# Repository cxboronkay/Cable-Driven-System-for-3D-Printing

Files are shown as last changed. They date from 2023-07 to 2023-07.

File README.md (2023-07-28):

# Cable-Driven-System-for-3D-Printing
Please see the powerpoint "Large scale 3d printing with CDPR" for instructional information and electronics schematics before use.

Design files and necessary programs for running the CDPR machine can be found here, as well as simple example G-code programs. Assembly is uploaded as a SolidWorks assembly with all necessary parts. All 3D printed parts are also uploaded as STEPs and STLs, as well as one STEP version of the assembly as a whole.
CDPRassem


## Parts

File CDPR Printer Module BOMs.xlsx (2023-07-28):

Single Pulley Module
Part Name | Qty | Process/Material | Remark
Table base | 1 | 3D printed (PLA)
5mm Flanged Bearing (16mm OD) | 1 | -
Small scale pulley | 1 | 3D printed (PLA)
Pulley mount | 2 | 3D printed (PLA) | Designed for PLA although mine were printed in PETG
6mm flanged bearing (13mm OD) | 2 | -
Encoder mount | 1 | 3D printed (PLA)
6mm d-shaft (L 55mm) | 1 | 3D printed (PLA) | Steel shaft can be purchased but often run oversized for fitting in bearing
Rope guide | 1 | 3D printed (PLA)
AS5600 magnetic encoder | 1 | - | and accompanying magnet (will be fixed to end of shaft)
M5 eyebolt (L 3.5 cm) | 1 | -
6mm washers (1.2mm thickness) | 6 | Nylon
M5 socket head bolt (L 16mm) | 9 | -
M5 socket head bolt (L 18mm) | 3 | -
M3 screw (L 5mm) | 2 | -
M5 washers (1mm thickness) | 8 | Nylon | Or can use equivalent 8mm spacer
M5 washers | 7 | Steel
M5 hex nuts | 13 | -
M3 hex nuts | 2 | -
M5 extrusion insert nut | 1 | - | If mounting module to aluminum extrusion
Single Winch Module
Part Name | Qty | Process/Material | Remark
NEMA 17 stepper motor | 1 | -
Motor mount | 1 | 3D printed (PLA)
Winch bearing mount | 1 | 3D printed (PLA)
2020 T-slot profile bar (L 60mm) | 1 | Aluminum
5mm to 8mm shaft coupler | 1 | -
8mm flanged bearing (16mm OD) | 1 | -
Winch spool | 1 | 3D printed (PLA)
8mm d-shaft (L 55mm) | 1 | 3D printed (PLA)
M5 eyebolt (L 3.5 cm) | 1 | -
Extrusion corner bracket | 1 | -
M8 washer (1.4mm thickness) | 1 | Nylon
M5 bolt (L 8mm) | 8 | -
M5 extrusion insert nut | 9 | - | If mounting module to aluminum extrusion
M3 screw (L 10mm) | 2 | -

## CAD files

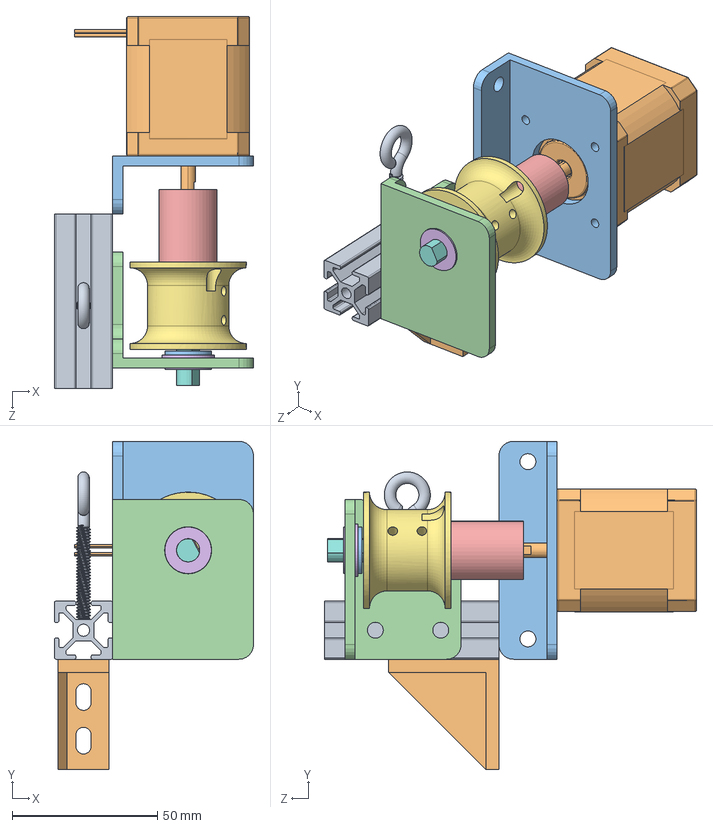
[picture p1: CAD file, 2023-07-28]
SW Design Files/Winch module.SLDASM
68.5 x 113.0 x 128.0 mm
2020 T-slot profile bar
NEMA motor 17HS19-2004S1
motor (NEMA) mount
winch bearing mount
5mm to 8mm coupler
8mm flange bearing
winch spool 2
8mm d shaft
M5 eyebolt (stand-in)
6mm corner bracket
M8 nylon washer

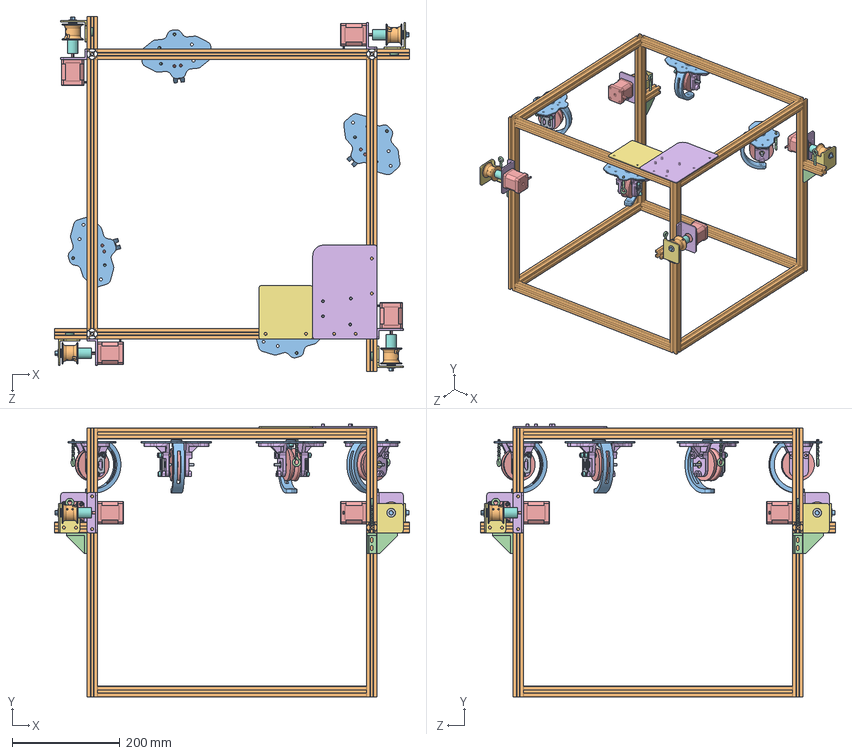
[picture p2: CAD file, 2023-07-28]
SW Design Files/CDPR printer assembly.SLDASM
660.0 x 507.5 x 660.0 mm
2020 T-slot profile bar x 16
table_base_v4 x 4
5mm flanged bearing x 4
Small-scale pulley x 4
Pulley mount x 8
6mm flanged linear x 8
Encoder mount AS5600 x 4
91290A238_Alloy Steel Socket Head Screw x 16
6mm d-shaft x 4
5mm hex nut x 12
ropeguide_v3 x 4
M5 eyebolt (stand-in) x 8
NEMA motor 17HS19-2004S1 x 4
motor (NEMA) mount x 4
winch bearing mount x 4
5mm to 8mm coupler x 4
8mm flange bearing x 4
winch spool 2 x 4
8mm d shaft x 4
6mm corner bracket x 4
M8 nylon washer x 4
electronics_board
second_electronics_board

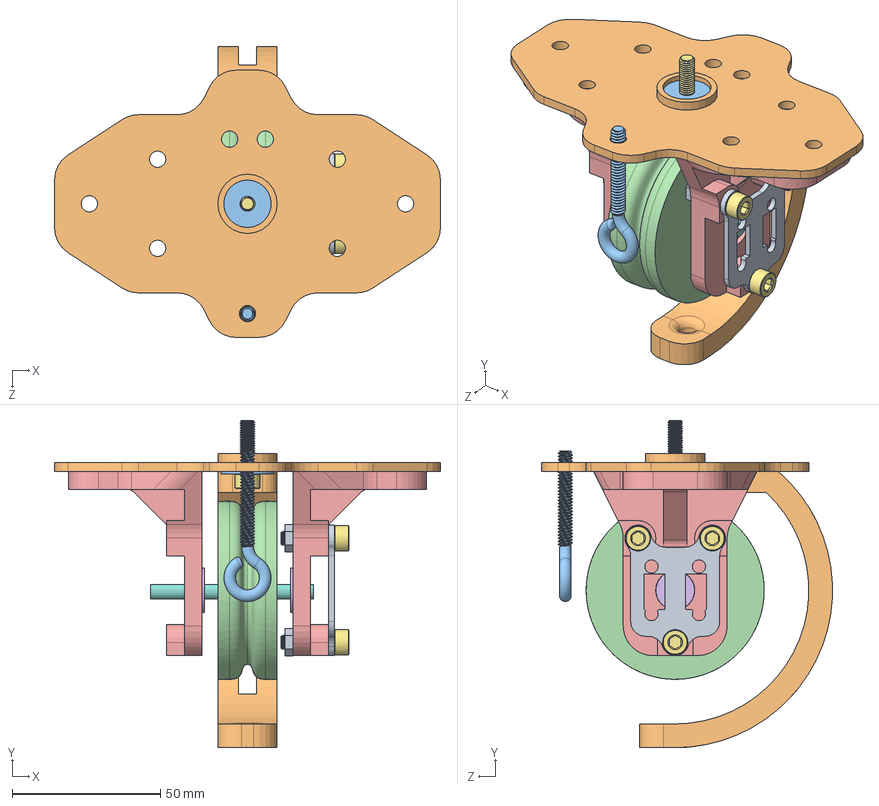
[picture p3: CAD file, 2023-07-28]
SW Design Files/Pulley encoder module.SLDASM
130.0 x 110.2 x 97.9 mm
table_base_v4
5mm flanged bearing
Small-scale pulley
Pulley mount x 2
6mm flanged linear x 2
Encoder mount AS5600
91290A238_Alloy Steel Socket Head Screw x 4
6mm d-shaft
5mm hex nut x 3
ropeguide_v3
M5 eyebolt (stand-in)

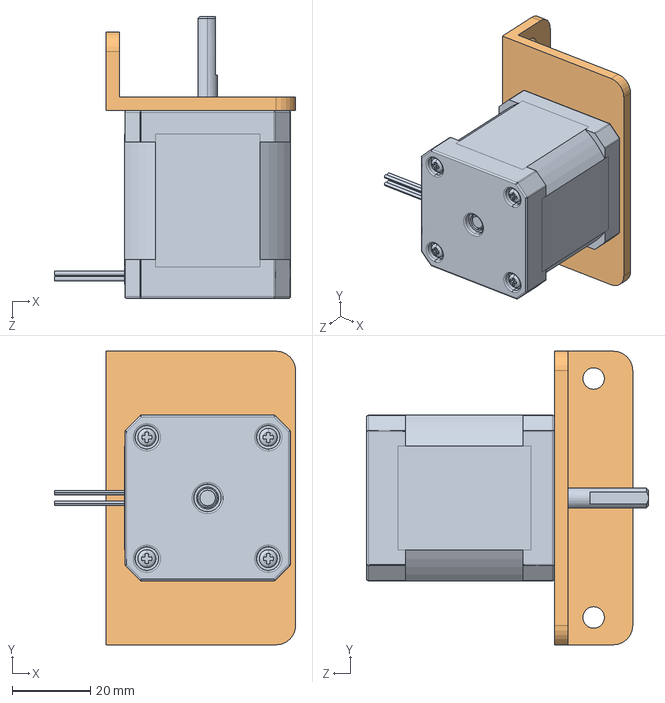
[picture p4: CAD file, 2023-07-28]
SW Design Files/motor assembly.SLDASM
61.7 x 75.0 x 72.0 mm
NEMA motor 17HS19-2004S1
motor (NEMA) mount

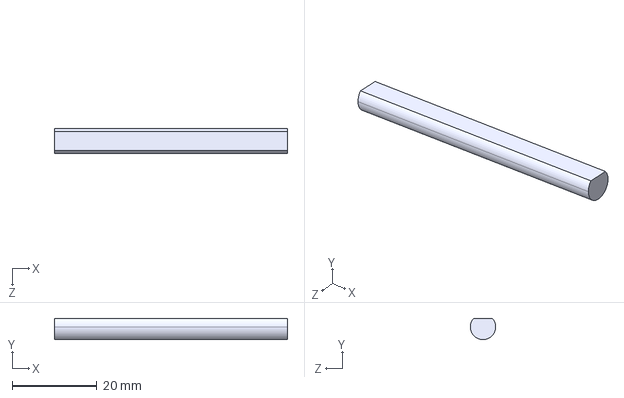
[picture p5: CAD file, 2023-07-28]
STEP files/6mm d-shaft.STEP
55.0 x 5.00 x 6.00 mm

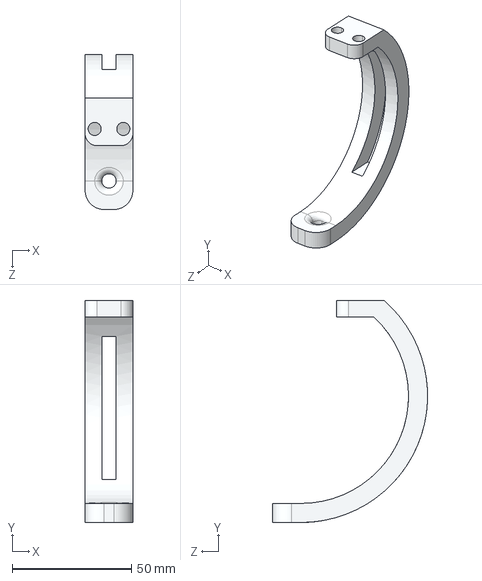
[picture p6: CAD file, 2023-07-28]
STEP files/ropeguide_v3.STEP
20.0 x 93.0 x 65.0 mm

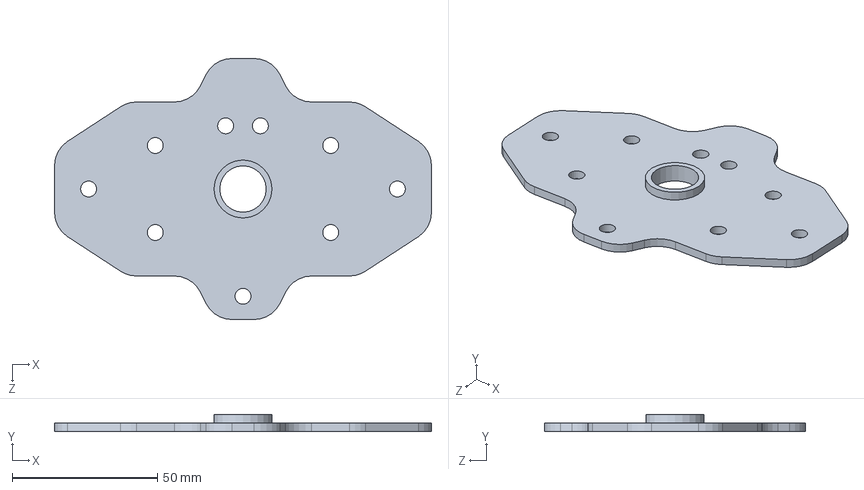
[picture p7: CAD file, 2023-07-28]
SW Design Files/table_base_v4.SLDPRT
130.0 x 6.00 x 90.0 mm

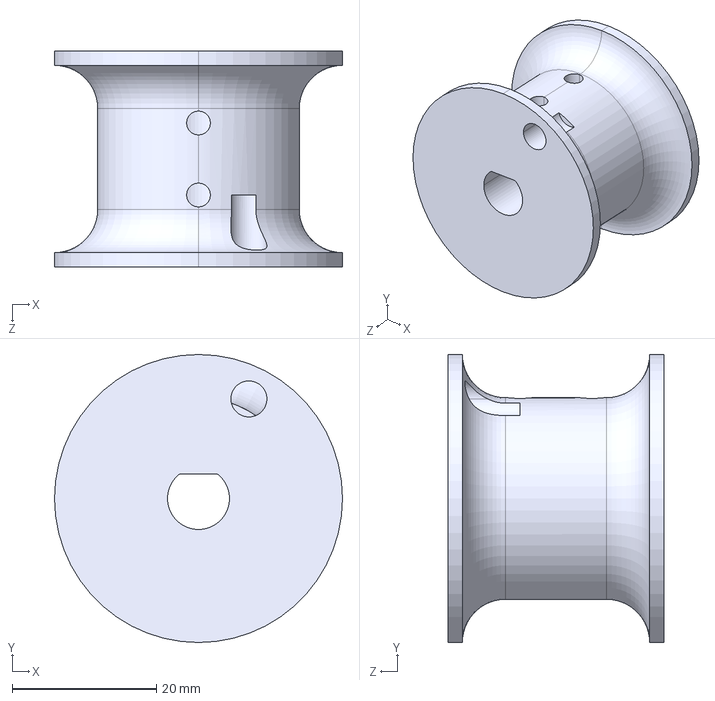
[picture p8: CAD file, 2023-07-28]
STEP files/winch spool 2.STEP
40.0 x 40.0 x 30.0 mm

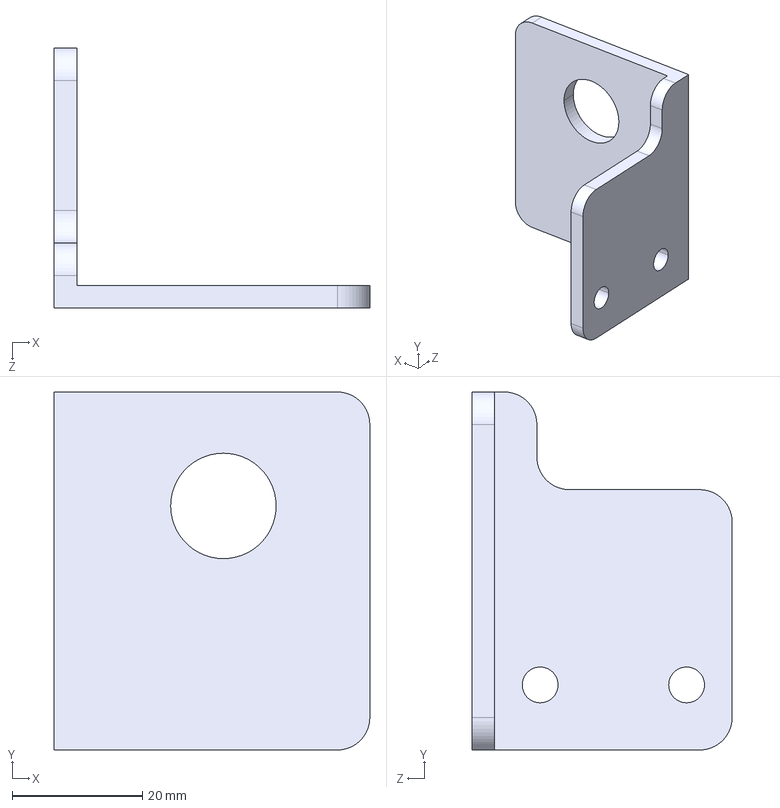
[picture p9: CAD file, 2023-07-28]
STEP files/winch bearing mount.STEP
48.5 x 55.0 x 40.0 mm

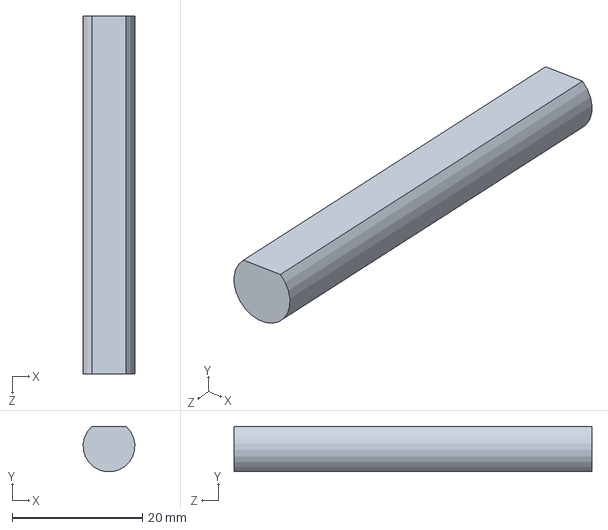
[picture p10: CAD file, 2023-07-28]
SW Design Files/8mm d shaft.SLDPRT
7.95 x 6.97 x 55.0 mm

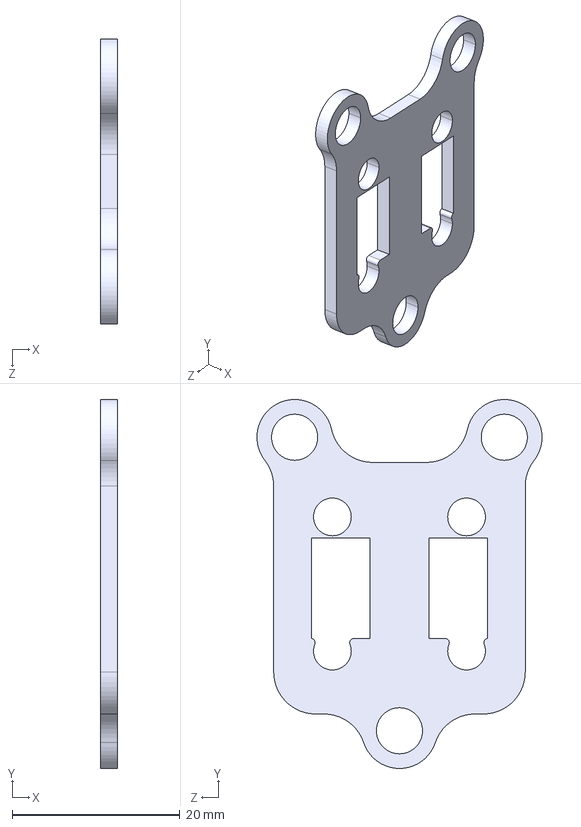
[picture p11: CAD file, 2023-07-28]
STEP files/Encoder mount AS5600.STEP
2.00 x 44.0 x 34.0 mm

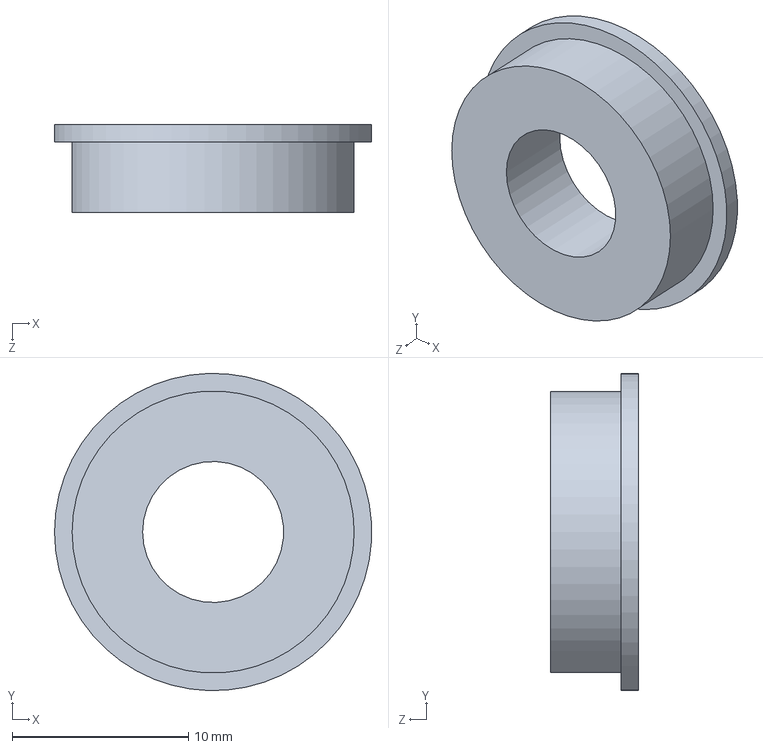
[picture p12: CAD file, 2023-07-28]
SW Design Files/8mm flange bearing.SLDPRT
18.0 x 18.0 x 5.00 mm

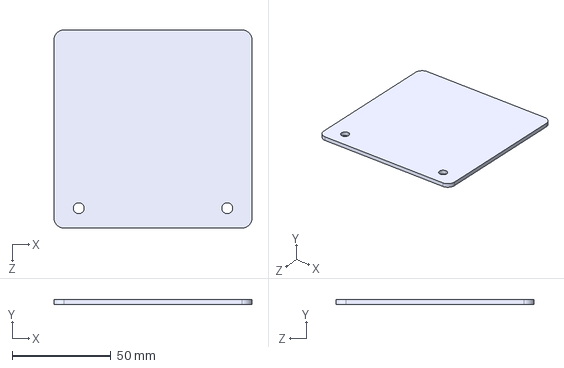
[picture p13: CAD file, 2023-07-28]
STEP files/second_electronics_board.STEP
100.0 x 2.50 x 100.0 mm

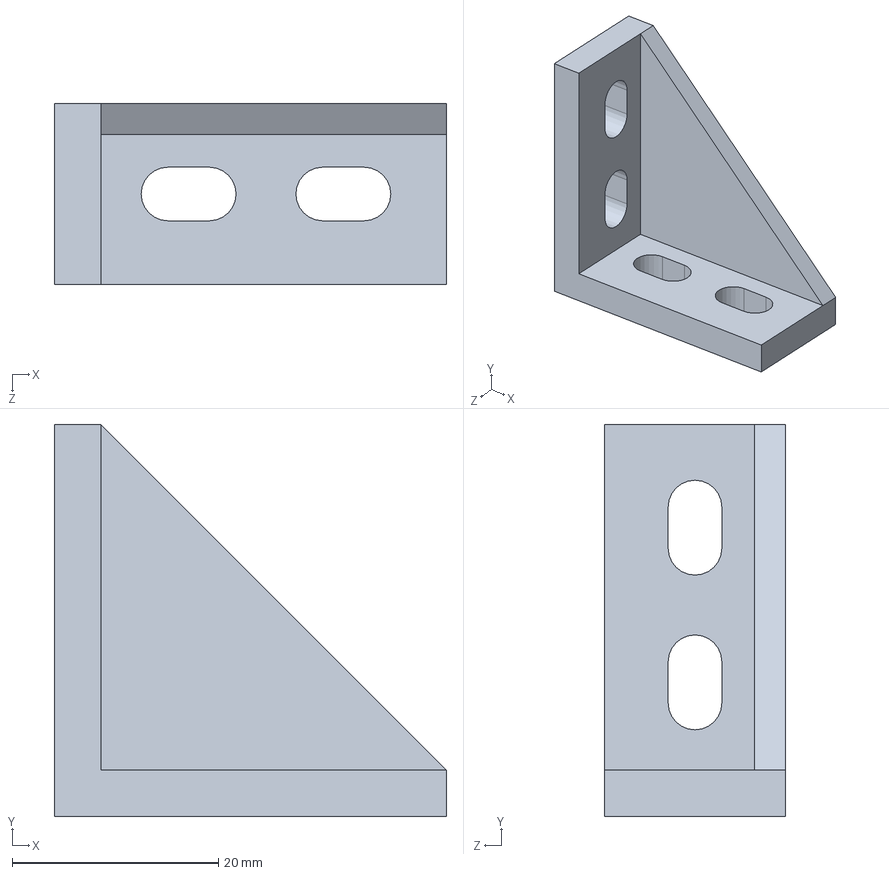
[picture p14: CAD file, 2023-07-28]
SW Design Files/6mm corner bracket.SLDPRT
38.0 x 38.0 x 17.5 mm

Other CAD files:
SW Design Files/6mm d-shaft.SLDPRT
SW Design Files/winch spool 2.SLDPRT
SW Design Files/Encoder mount AS5600.SLDPRT
STEP files/table_base_v4.STEP
STEP files/8mm d shaft.STEP
STEP files/Pulley mount.STEP
STEP files/Small-scale pulley.STEP
STEP files/electronics_board.STEP
STEP files/motor (NEMA) mount.STEP
STL Files/6mm d-shaft.STL
STL Files/8mm d shaft.STL
STL Files/Encoder mount AS5600.STL
STL Files/Pulley mount.STL
STL Files/Small-scale pulley.STL
STL Files/electronics_board.STL
STL Files/motor (NEMA) mount.STL
STL Files/ropeguide_v3.STL
STL Files/second_electronics_board.STL
STL Files/table_base_v4.STL
STL Files/winch bearing mount.STL
STL Files/winch spool 2.STL
SW Design Files/2020 T-slot profile bar.SLDPRT
SW Design Files/5mm flanged bearing.SLDPRT
SW Design Files/5mm hex nut.SLDPRT
SW Design Files/5mm to 8mm coupler.SLDPRT
SW Design Files/6mm flanged linear.SLDPRT
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

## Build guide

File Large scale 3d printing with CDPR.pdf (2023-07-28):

# Large scale 3d printing with CDPR

Cadence Boronkay

# Research, planning, scope

# Design goals + constraints

- Scalable
- Modular for in situ applications
- Precision satisfactory for 3d printing
- Visually/aesthetically appealing

# Previous work

- CDPR robots have been used at large scales (eg. construction), but typically for pick and place purposes, rather than additive manufacturing.
- Some 3d CDPR printers have been built at smaller scales, and with less modularity (fully constrained, many cables, fixed winch locations).
- There is a literature available on fully constrained CDPR printers but much less on underactuated (cable suspended) CDPRs.

# CDPR constraining

- m = number of cables, n = degrees of freedom
- m < n + 1 : under-constrained/underactuated (cable suspended)
- m = n + 1 : fully constrained
- m > n + 1 : redundantly constrained
- For 6 DOFs (full control of position and orientation), 8 cables are typically used.
- This is more complex, as one must avoid cable-cable and cable-end effector interference.

# CDPR constraining (cable arrangements)

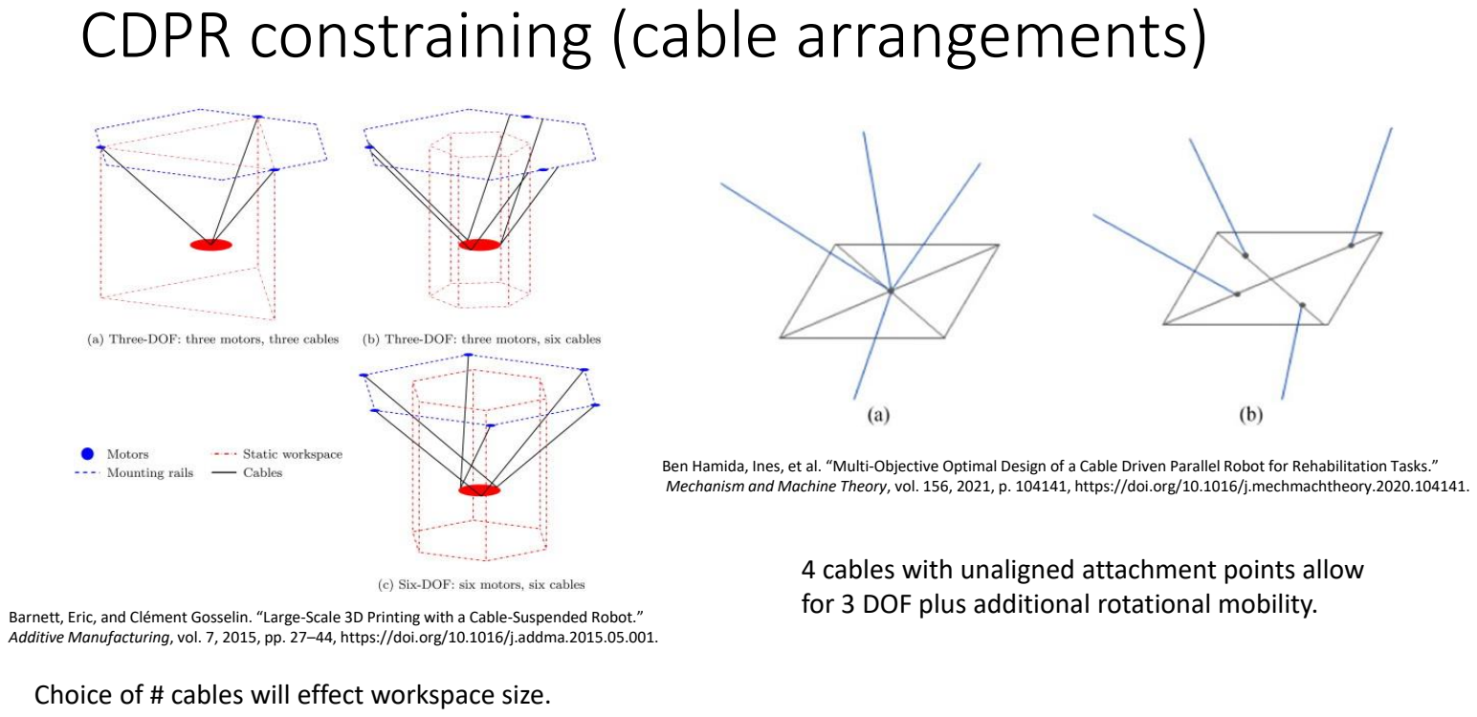
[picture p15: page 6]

Barnett, Eric, and Clément Gosselin. “Large-Scale 3D Printing with a Cable-Suspended Robot.” Additive Manufacturing, vol. 7, 2015, pp. 27–44, https://doi.org/10.1016/j.addma.2015.05.001.

Ben Hamida, Ines, et al. “Multi-Objective Optimal Design of a Cable Driven Parallel Robot for Rehabilitation Tasks.” Mechanism and Machine Theory, vol. 156, 2021, p. 104141, https://doi.org/10.1016/j.mechmachtheory.2020.104141.

4 cables with unaligned attachment points allow for 3 DOF plus additional rotational mobility.

Choice of # cables will effect workspace size.

# Controls

- Encoder options
- Encoder on motor/winch (will have error due to irregular winch diameter from cable spooling)
- *Rotary encoder on pulley (requires no cable slip on pulley, nonaxial forces due to the pulley on the encoder shaft could be problematic)
- Draw wire/cable pull encoder (limits scale-up, maximum draw length of encoder determines possible cable travel).
- Still researching software options for trajectory control/path generation from G-code.
- WireX, Hangprinter…

# Initial design sketching

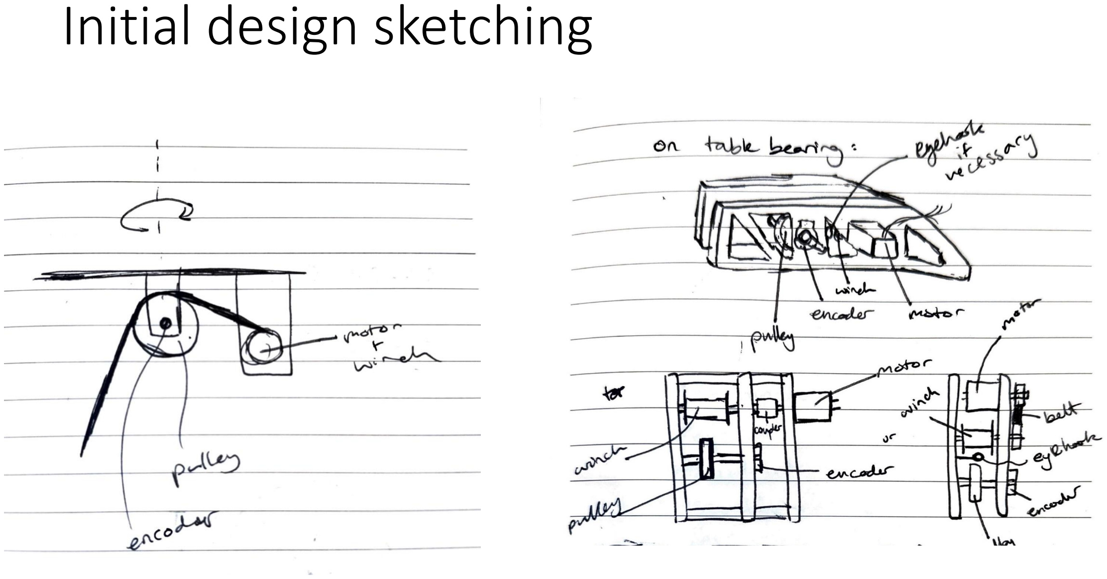
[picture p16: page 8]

# Design Considerations

- Pulley
- U-groove
- Eyehook to guide cable (prevent derailing)
- For encoder, cable must not slip on pulley (pulley needs to rotate with cable the entire time)
- Rubber coating? High traction material?
- If slippage is unavoidable, encoder could be moved to separate measuring wheel. (still need to somehow prevent slippage -> maybe dual-side wheels?)
- Check mechanical + dynamic calculations: need weight of end-effector, pulley material for friction coefficient, motor torque, etc.

# Design Considerations

- Turntable
- Probably best to put pulley on a table bearing - more accurate cable length measurements and less non-axial loads on cable and pulley. (Expected to be more significant on large-scale).
- Put entire module on turntable or just pulley?
- I think more entire is more modular and elegant, but possibly unnecessary).
- Table bearing axis of rotation needs to be centered above last point of contact (pulley) for controls. (Parametric measurements done from here too).

# Planning

- Small-scale prototype design, continue controls research
- Fabricate prototype, assembly 1 module (module = 1 set of motor/winch/pulley)
- Test module
- Revision
- Fabricate + assemble m modules
- Assemble m cable system
- Test system (small scale CDPR)
- Revise
- Work on scale-up of module

# Magnetic position encoder

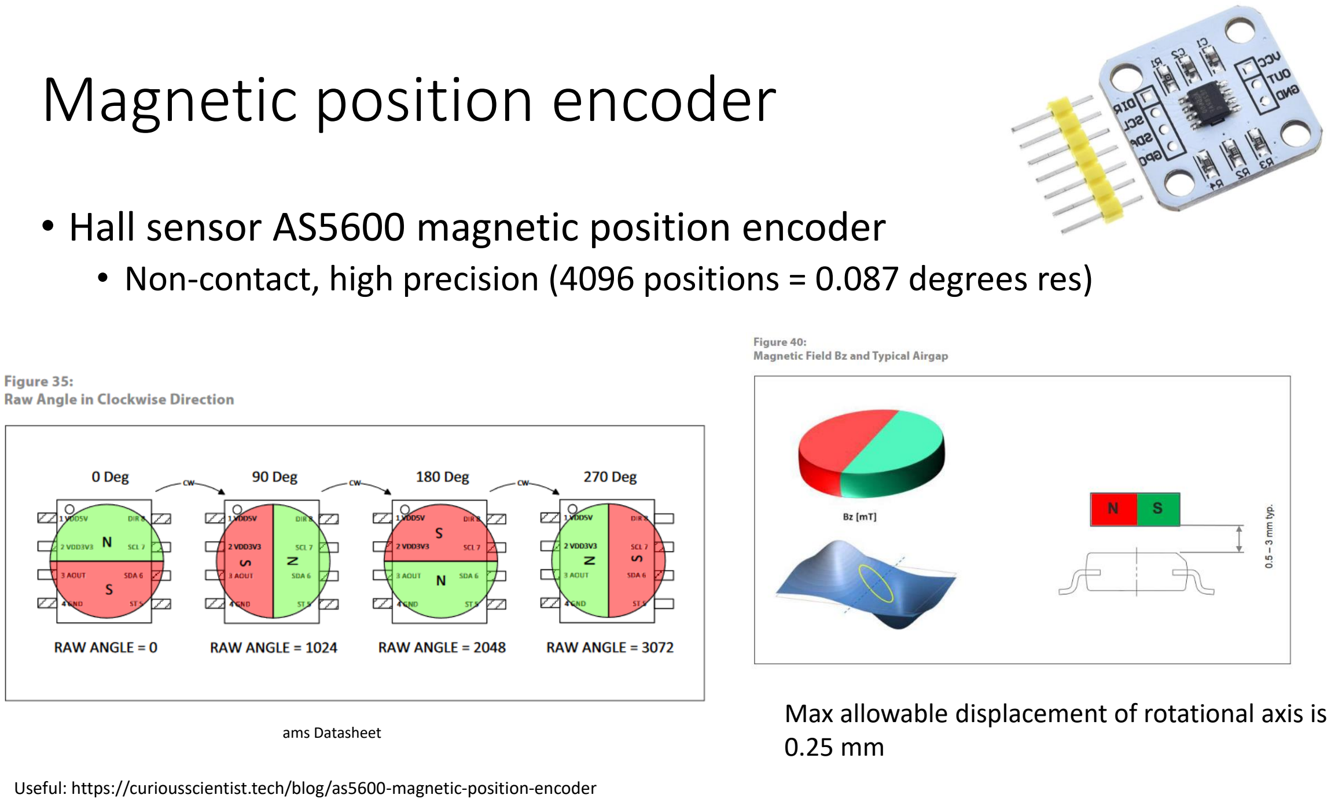
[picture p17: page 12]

- Hall sensor AS5600 magnetic position encoder
- Non-contact, high precision (4096 positions = 0.087 degrees res)

ams Datasheet

Max allowable displacement of rotational axis is 0.25 mm

Useful: https://curiousscientist.tech/blog/as5600-magnetic-position-encoder

# Mechanical Design

Small-scale version of CDPR mechanism

# Pulley module

- Pulley for rope (currently thin string) needs to have enough friction to prevent slippage between string and pulley, as slippage would cause tracking error with the encoder.
- Need string exit point to be fixed. Since these pulleys rotate, the exit point is directly below the rotational axis such that rotation does not effect where the string ends contact with the module. (However, with both the rope guide and the eyebolt, it seems unnecessary to have the ability to rotate).
- Magnet for encoder is glued to the end of the shaft. Must be concentric and within 1

-3mm
of the encoder itself.

Encoder
mount
(encoder
is
attached
to inner
face)

Rotational
axis

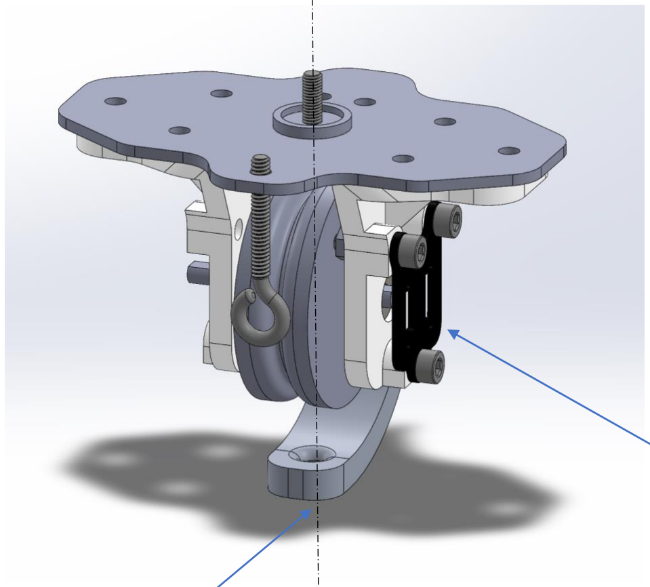
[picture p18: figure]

String exit
point

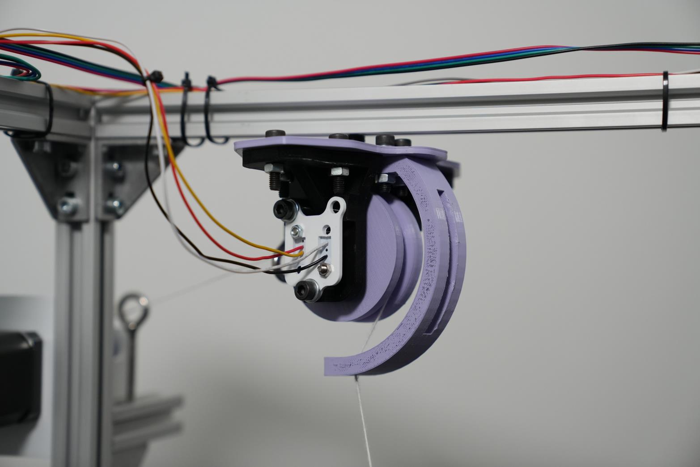
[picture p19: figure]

# Pulley module BOM

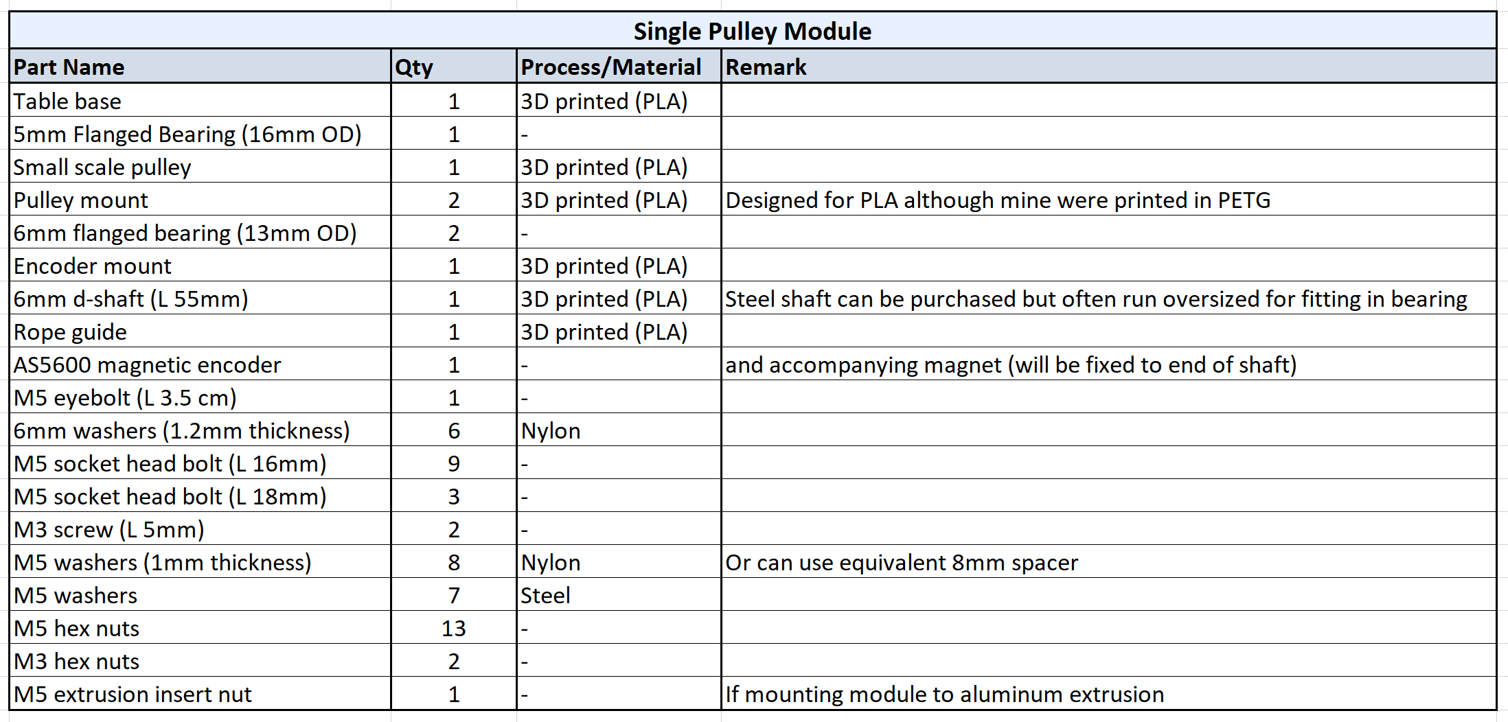
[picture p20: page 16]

# Winch module

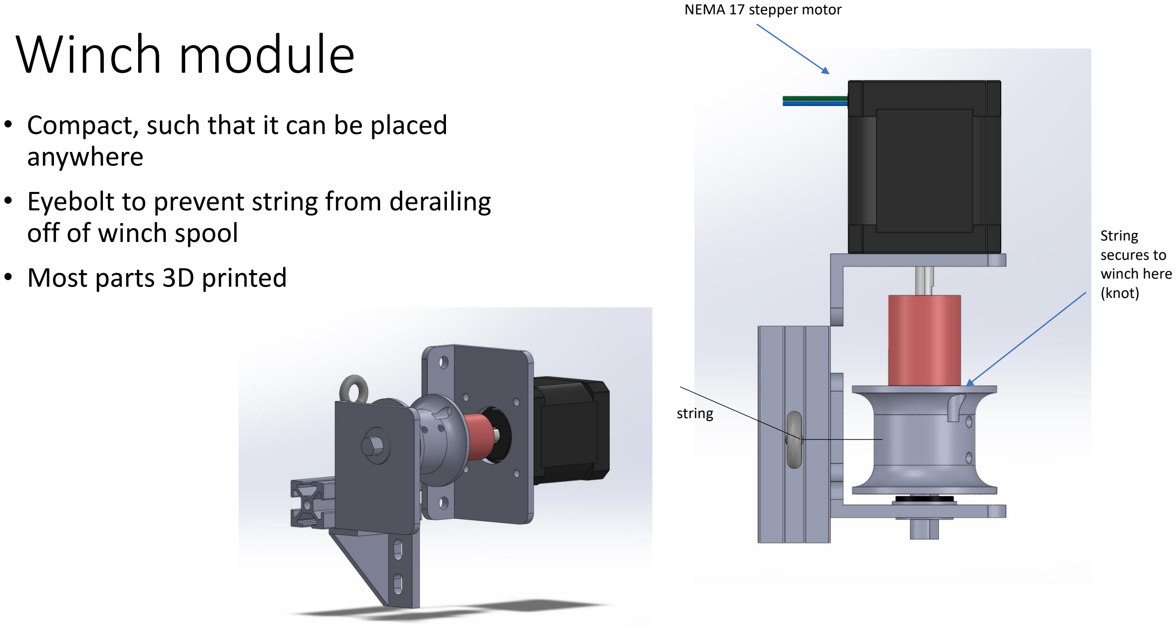
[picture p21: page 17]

- Compact, such that it can be placed anywhere
- Eyebolt to prevent string from derailing off of winch spool
- Most parts 3D printed

String
secures to
winch here
(knot)

string

NEMA 17 stepper motor

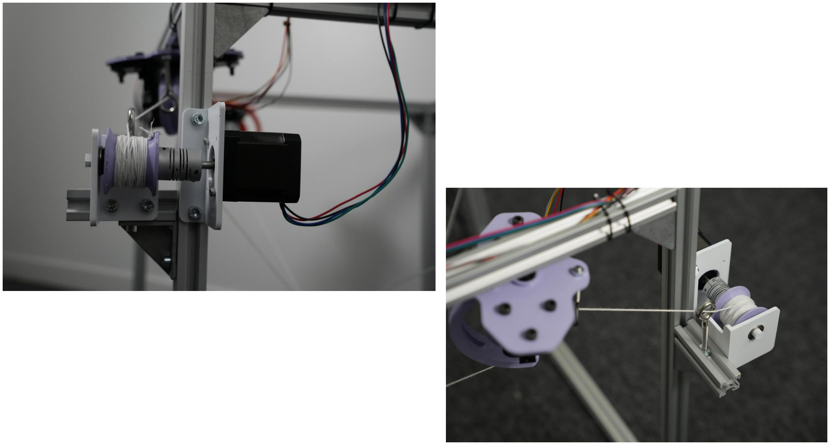
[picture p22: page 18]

# Winch module BOM

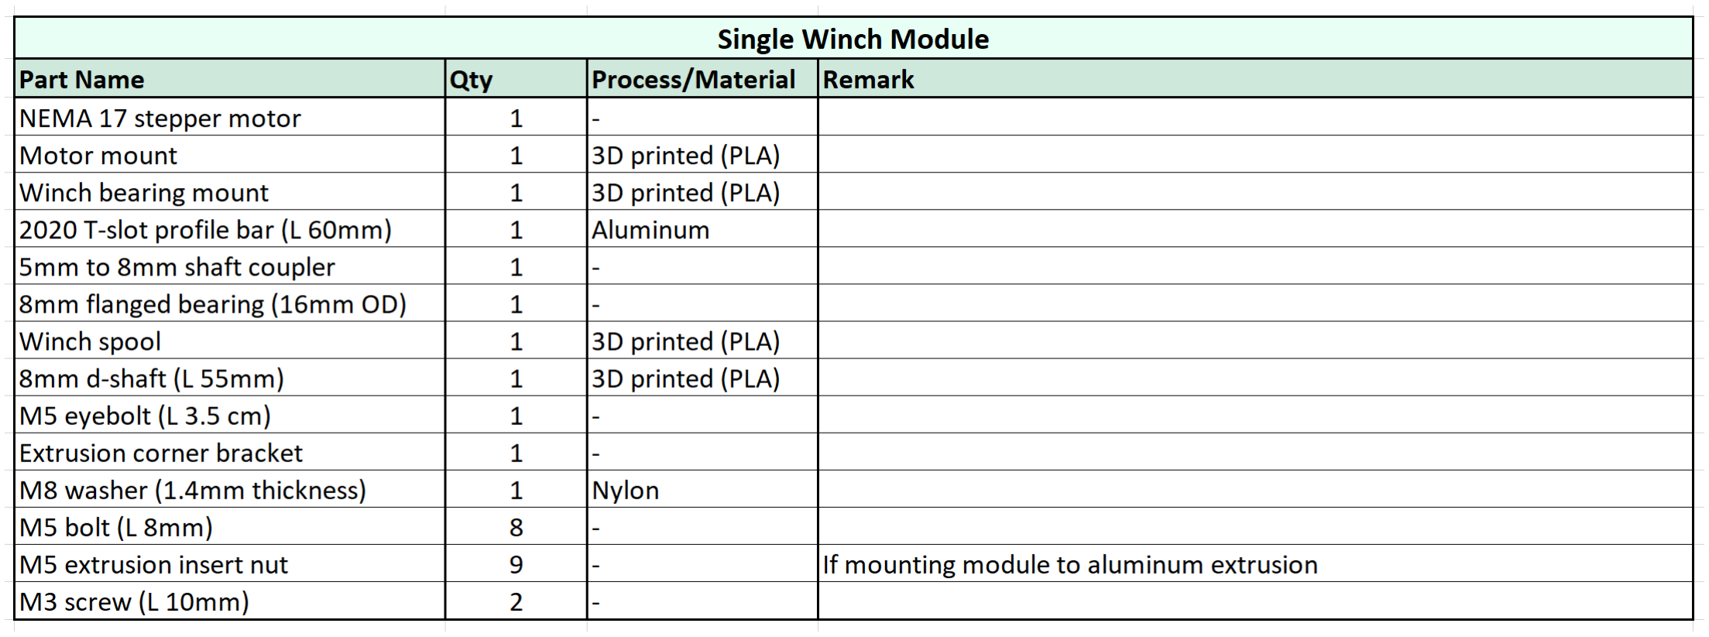
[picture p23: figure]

# Structural schematic

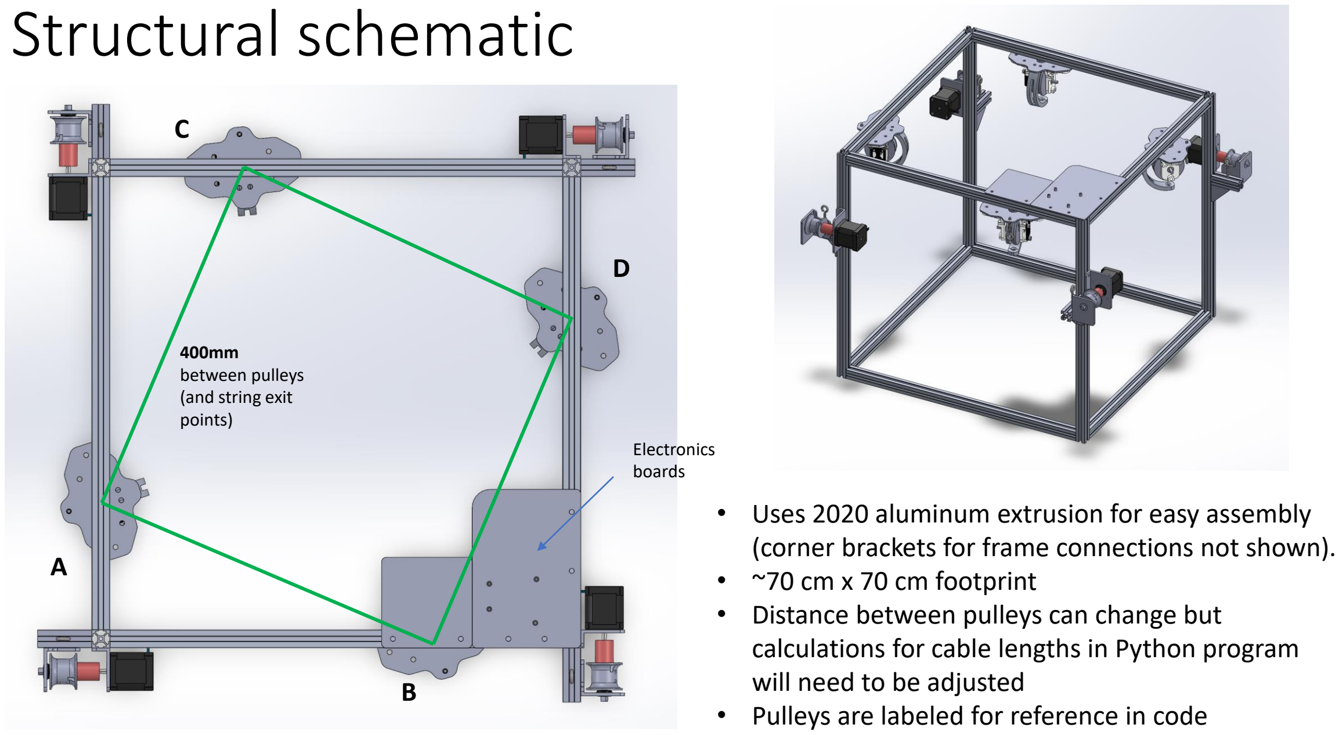
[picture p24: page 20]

400mm
between pulleys
(and string exit
points)
- Uses 2020 aluminum extrusion for easy assembly (corner brackets for frame connections not shown).
- ~70 cm x 70 cm footprint
- Distance between pulleys can change but calculations for cable lengths in Python program will need to be adjusted
- Pulleys are labeled for reference in code

Electronics
boards

A

B

C

D

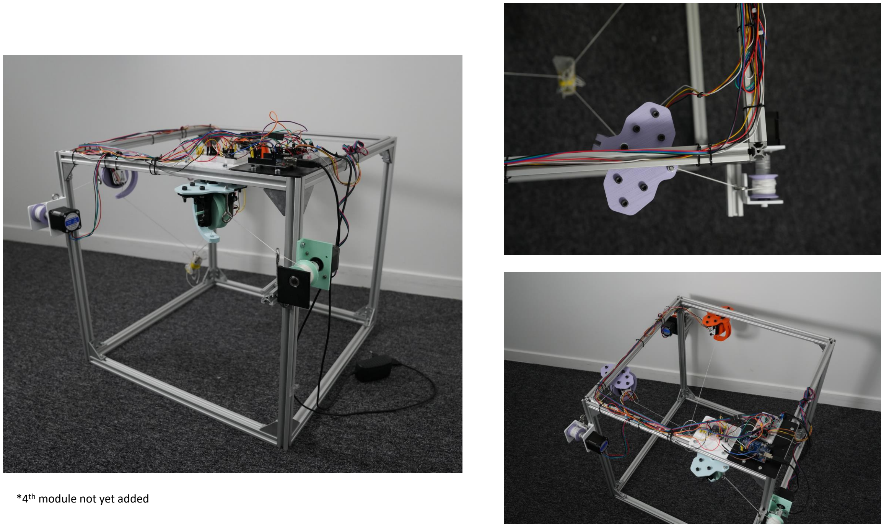
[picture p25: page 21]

*4th module not yet added

# Electronics/hardware

# Components

- Arduino Uno
- A4988 stepper motor drivers (1 per motor)
- AS5600 magnetic encoder (1 per pulley)
- I2C multiplexer
- 100 µF capacitor
- 12V power supply

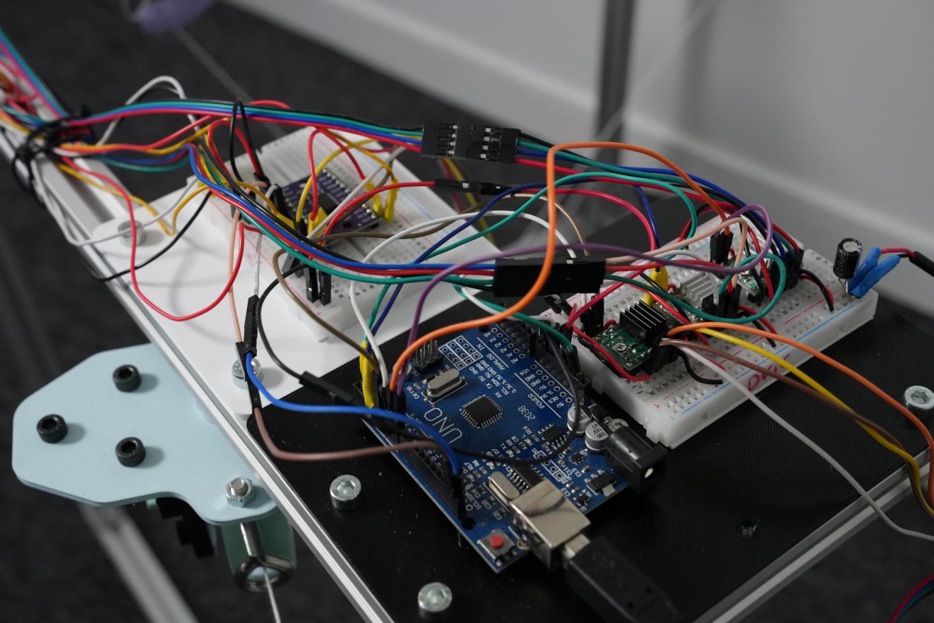
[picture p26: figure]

# I2C and encoders schematic

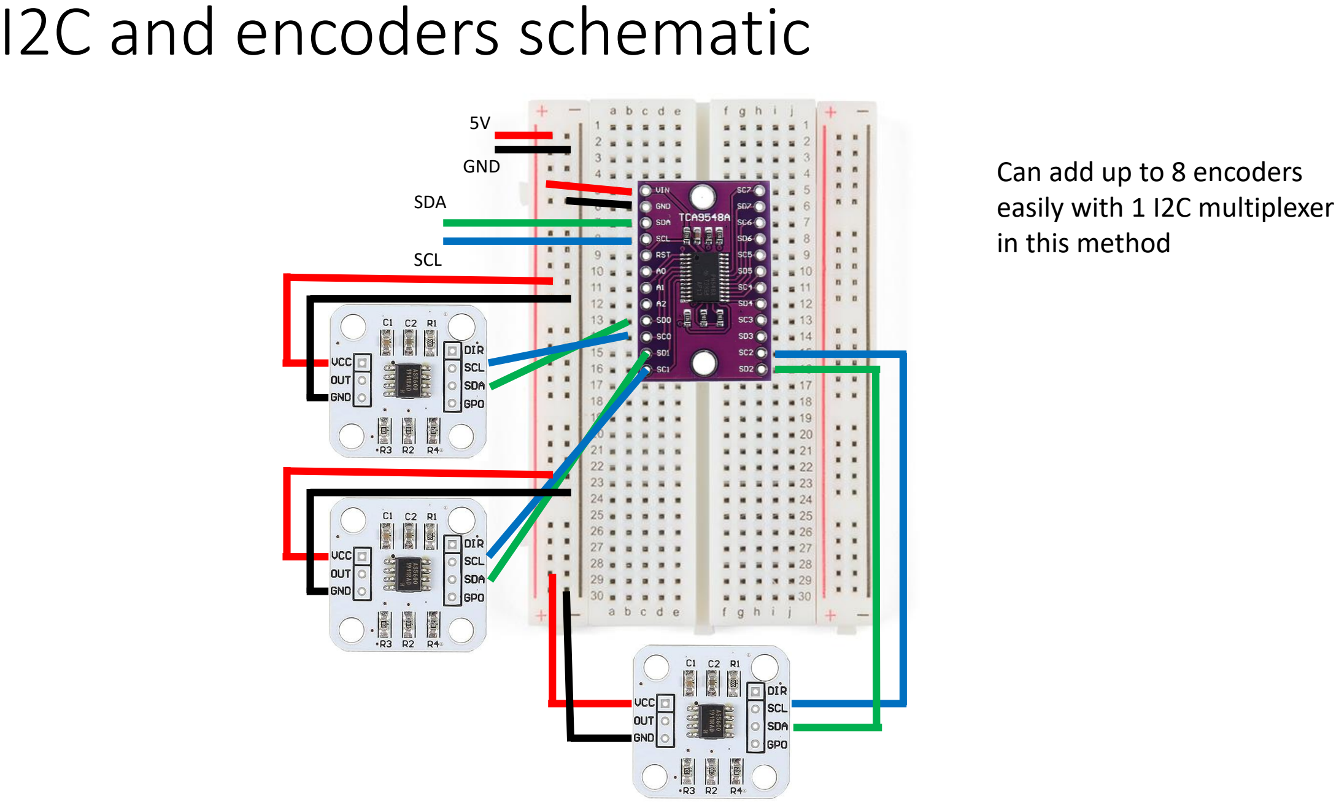
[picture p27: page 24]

5V

GND

SDA

SCL

Can add up to 8 encoders
easily with 1 I2C multiplexer in this method

# Motor driver schematic

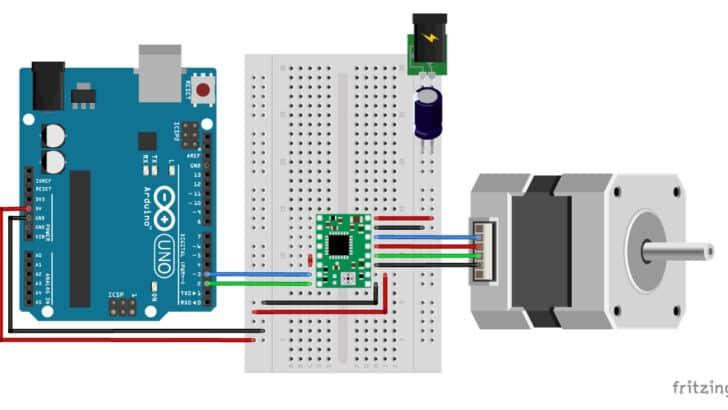
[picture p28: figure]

https://www.makerguides.com/a4988-stepper-motor-driver-arduino-tutorial/ (https://www.makerguides.com/a4988-stepper-motor-driver-arduino-tutorial/)

- Add motor drivers
and motors with
same connections
- Do not plug/unplug
motors when 12V
power supply is
connected and on!

# Software

# Converting G-code to cable length coordinates

- Python program: gcode_to_ourcoords.py
reads a G-code txt file and outputs a string of coordinates that can be copied into the Arduino sketch to control the pulley system.
- It also outputs the number of coordinates, which will need to be set in the Arduino sketch.
- Currently works best with not too long, cleaned up G-code (removing non-coordinate G-code lines/commands)
- Calculation section will need to be adjusted for different pulley configurations (eg. different distance between pulleys)
- Python program and example G-code can be found in GitHub repository: https://github.com/cxboronkay/Cable-Driven-System-for-3D-Printing (https://github.com/cxboronkay/Cable-Driven-System-for-3D-Printing)

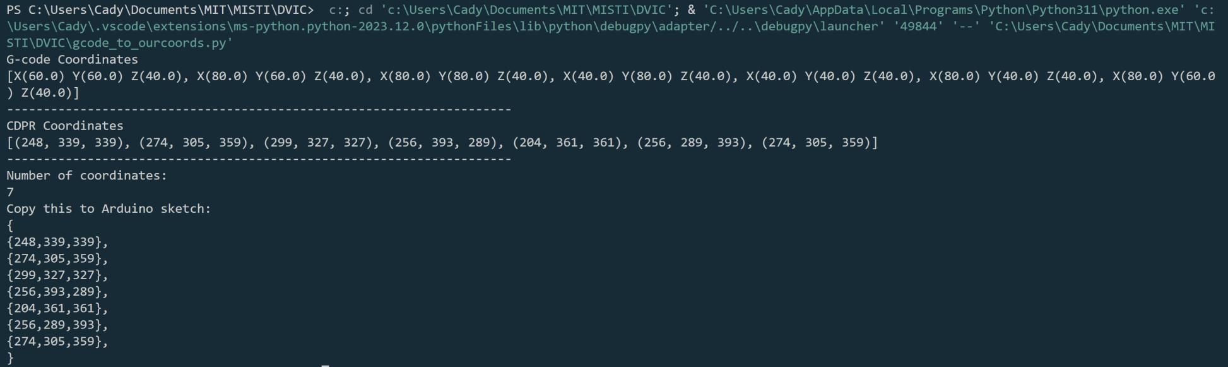
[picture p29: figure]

# Controlling the machine

- Arduino sketch for performing trajectory described by translated G-code coordinates: run_gcode_3pulley.ino
- Copy coordinates from python program where indicated. Also adjust numcoords value and the initiation length for the coordinates list.
- Manually rotate winches to position end effector at the starting position noted in the sketch (originally 200, 350, 350 mm).
- Once uploaded to Arduino, begin Serial and turn on 12V power. There is an intentional 10 second delay before it will begin to move (can be shortened or removed if desired). It will then move to each coordinate in the list before stopping.
- Next location, current coordinates, and speeds will all appear in the Serial print out.
- Pulleys A, B, and C refer to the same pulleys noted in the structural schematic shown in the Mechanical Design section.
- https://github.com/cxboronkay/Cable-Driven-System-for-3D-Printing

# Future steps

# Next

- To get closer to the end goal of a large-scale CDPR 3D printer, next steps include:
- Adding 4th pulley to gain another degree of freedom (be able to partially control angle of end effector).
- Improve software and control over trajectories.
- Scale up to be able to support the 3D printing nozzle.
- Make design more modular (mountable to anything, sturdier, etc.)

# Thank you!!

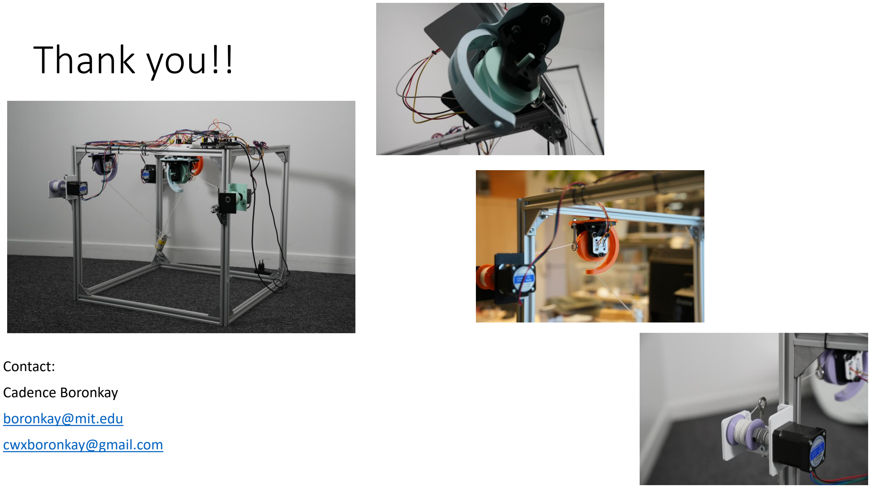
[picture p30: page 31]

Contact:
Cadence Boronkay
boronkay@mit.edu
cwxboronkay@gmail.com

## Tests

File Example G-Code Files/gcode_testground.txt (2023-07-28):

G1 X40 Y40 Z-33
G1 Y60
G1 X60
G1 Y40
G1 X40

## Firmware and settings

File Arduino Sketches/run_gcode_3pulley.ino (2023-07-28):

// Takes converted G-Code coordinates and moves through all coordinates then stops.

// Include I2C, encoder, math, and AccelStepper libraries:
#include <Wire.h>
#include <AS5600.h>
#include <math.h>
#include <AccelStepper.h>

// Create encoder instances:
AS5600 encoderA;
AS5600 encoderB;
AS5600 encoderC;

// Define I2C address:
#define TCAADDR 0x70
// Initialize variables for position monitoring:

void tcaselect (uint8_t i) {
  if (i > 7) return;

  Wire.beginTransmission(TCAADDR);
  Wire.write(1 << i);
  Wire.endTransmission();
}

// Create variables:
int speedA;
int speedB;
int speedC;
int requestedLocation[3]; // in millimeters
float currentPosition[3];
float currentLocation[3];
float startLength[3] = {200, 350, 350}; // need to manually move end effector here before starting Serial!!
float pulleyRadius = 26.25; //in mm
float positionDiff[3];
float locationDiff[3];
float output[3];
float lastOutput[3];
float initPosition[3];
float position[3];
float revolutions[3] = {0,0,0};
float printLength[3];
int counter = 0;
int numcoords = 42;    //number of coordinates being inputted (can get from python program)  **Don't forget to change when changing coordinate list!!**

// Define stepper motor connections and motor interface type (1 when using driver):

#define dirPinA 3
#define stepPinA 2
#define motorInterfaceTypeA 1


#define dirPinB 5
#define stepPinB 4
#define motorInterfaceTypeB 1

#define dirPinC 7
#define stepPinC 6
#define motorInterfaceTypeC 1

// Create new instances of AccelStepper class:
AccelStepper stepperA = AccelStepper(motorInterfaceTypeA, stepPinA, dirPinA); //PULLEY A
AccelStepper stepperB = AccelStepper(motorInterfaceTypeB, stepPinB, dirPinB); //PULLEY B
AccelStepper stepperC = AccelStepper(motorInterfaceTypeC, stepPinC, dirPinC); //PULLEY C

// Copy translated coordinates here:
int coordinate_list[42][3] =         //**Don't forget to adjust first integer for number of coordinates**
 {
{273,435,313},
{265,437,320},
{258,437,328},
{250,434,337},
{247,432,342},
{244,430,347},
{241,427,352},
{239,424,357},
{235,416,366},
{234,412,371},
{233,407,375},
{233,401,381},
{234,392,387},
{236,382,392},
{241,371,397},
{250,358,399},
{256,351,399},
{260,348,398},
{263,345,396},
{267,343,395},
{271,342,393},
{274,341,390},
{278,340,387},
{281,340,384},
{287,342,378},
{290,344,373},
{295,349,365},
{301,361,350},
{303,370,340},
{304,380,330},
{303,389,323},
{303,394,320},
{302,399,316},
{300,404,313},
{299,408,311},
{297,413,309},
{294,417,308},
{292,421,307},
{287,426,307},
{283,430,308},
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
    {200,350,350}         //Can be convenient to add homing coordinate at end of program to return cables to original lengths (Don't forget to add 1 to the numcoords).
  };

//------------------------------------------------------------------------------------------------
void setup() {
  // Begin serial communication:
  Serial.begin(115200);
  
  // Set the maximum speed in steps per second:
  stepperA.setMaxSpeed(2000);
  stepperB.setMaxSpeed(2000);
  stepperC.setMaxSpeed(2000);
  
  // Find initial encoder values for zeroing:
  tcaselect(0);
  output[0] = encoderA.getPosition();
  initPosition[0] = output[0];
  lastOutput[0] = output[0];
  position[0] = output[0];

  tcaselect(1);
  output[1] = encoderB.getPosition();
  initPosition[1] = output[1];
  lastOutput[1] = output[1];
  position[1] = output[1];


  tcaselect(2);
  output[2] = encoderC.getPosition();
  initPosition[2] = output[2];
  lastOutput[2] = output[2];
  position[2] = output[2];

}

//------------------------------------------------------------------------------------------------
void loop() {
  for(int i=0; i<3; i++)  {
    requestedLocation[i] = coordinate_list[counter][i];  
    Serial.println(requestedLocation[i]);
  }
  if (counter == 0){
    delay(10000);         //  remove or adjust if you do not want delay at start
  }
  boolean flagA = false;
  boolean flagB = false;
  boolean flagC = false;
  while (flagA == false || flagB == false || flagC == false){  
    // Monitor encoder position
    tcaselect(0);                             // get the raw values of the encoders
    output[0] = encoderA.getPosition();           
    tcaselect(1);
    output[1] = encoderB.getPosition();
    tcaselect(2);
    output[2] = encoderC.getPosition();

    if ((lastOutput[0] - output[0]) > 2047 )       // check if a full rotation has been made
      revolutions[0]++;
    if ((lastOutput[0] - output[0]) < -2047 )
      revolutions[0]--;
    if ((lastOutput[1] - output[1]) > 2047 )        
      revolutions[1]++;
    if ((lastOutput[1] - output[1]) < -2047 )
      revolutions[1]--;
    if ((lastOutput[2] - output[2]) > 2047 )        
      revolutions[2]++;
    if ((lastOutput[2] - output[2]) < -2047 )
      revolutions[2]--;
      
    currentPosition[0] = (-revolutions[0] * 4096 - output[0] + initPosition[0])* 0.087890625;   // calculate the position *IN DEGREES* the the encoder is at based off of the number of revolutions
    currentLocation[0] = startLength[0] + (currentPosition[0]/360)*2*M_PI*pulleyRadius;
    currentPosition[1] = (-revolutions[1] * 4096 - output[1] + initPosition[1])* 0.087890625;   // calculate the position *IN DEGREES* the the encoder is at based off of the number of revolutions
    currentLocation[1] = startLength[1] + (currentPosition[1]/360)*2*M_PI*pulleyRadius;
    currentPosition[2] = (-revolutions[2] * 4096 - output[2] + initPosition[2])* 0.087890625;   // calculate the position *IN DEGREES* the the encoder is at based off of the number of revolutions
    currentLocation[2] = startLength[2] + (currentPosition[2]/360)*2*M_PI*pulleyRadius;
    
    Serial.println("Location:");
    Serial.println(currentLocation[0]);
    Serial.println(currentLocation[1]);
    Serial.println(currentLocation[2]);
     
    lastOutput[0] = output[0];                      // save the last raw value for the next loop 
    lastOutput[1] = output[1];
    lastOutput[2] = output[2];
    
    // Set the speed in steps per second:
    speedA = -150;
    speedB = -150;
    speedC = -150;
    stepperA.setSpeed(speedA);
    stepperB.setSpeed(speedB);
    stepperC.setSpeed(speedC);
    // Run steppers until position reached
    locationDiff[0] = currentLocation[0] - requestedLocation[0];      // check length
    if (locationDiff[0] < 0) {
      speedA = -speedA;
      stepperA.setSpeed(speedA);
    }
    locationDiff[1] = currentLocation[1] - requestedLocation[1];      
    if (locationDiff[1] < 0) {
      speedB = -speedB;
      stepperB.setSpeed(speedB);
    }
    locationDiff[2] = currentLocation[2] - requestedLocation[2];      
    if (locationDiff[2] < 0) {
      speedC = -speedC;
      stepperC.setSpeed(speedC);
    }
    
    if (currentLocation[0] < (requestedLocation[0] + 1) && currentLocation[0] > (requestedLocation[0] - 1)){    //Stop if position is within requestedPosition bounds
      speedA = 0;
      stepperA.setSpeed(speedA);
      flagA = true;
    }
    if (currentLocation[1] < (requestedLocation[1] + 1) && currentLocation[1] > (requestedLocation[1] - 1)){    
      speedB = 0;
      stepperB.setSpeed(speedB);
      flagB = true;
    }    
    if (currentLocation[2] < (requestedLocation[2] + 1) && currentLocation[2] > (requestedLocation[2] - 1)){    
      speedC = 0;
      stepperC.setSpeed(speedC);
      flagC = true;
    }    
    stepperA.runSpeed(); //run stepper at set speed
    stepperB.runSpeed();
    stepperC.runSpeed();
    Serial.println("speedA:");
    Serial.println(speedA);
    Serial.println("speedB:");
    Serial.println(speedB);
    Serial.println("speedC:");
    Serial.println(speedC);
  }
  counter += 1;
//  delay(500);               // Uncomment for delay between coordinates
  if (counter == numcoords){      //Stop once at final coordinate
    Serial.println("DONE!!!!");
    delay(100000);
  }
}

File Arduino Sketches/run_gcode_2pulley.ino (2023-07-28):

// Takes converted G-Code coordinates and moves through all coordinates.

// Include I2C, encoder, math, and AccelStepper libraries:
#include <Wire.h>
#include <AS5600.h>
#include <math.h>
#include <AccelStepper.h>

// Create encoder instances:
AS5600 encoder0;
AS5600 encoder1;
//AS5600 encoder2;

// Define I2C address:
#define TCAADDR 0x70
// Initialize variables for position monitoring:

void tcaselect (uint8_t i) {
  if (i > 7) return;

  Wire.beginTransmission(TCAADDR);
  Wire.write(1 << i);
  Wire.endTransmission();
}

int speed0;
int speed1;
//int speed2;
int requestedLocation[2]; // in millimeters
float currentPosition[2];
float currentLocation[2];
float startLength[2] = {250, 250}; // need to manually move end effector here before starting Serial!!
float pulleyRadius = 26.25; //in mm
float positionDiff[2];
float locationDiff[2];
float output[2];
float lastOutput[2];
float initPosition[2];
float position[2];
float revolutions[2] = {0,0};
float printLength[2];
int counter = 0;
int numcoords = 147;

// Define stepper motor connections and motor interface type (1 when using driver):
#define dirPin0 3
#define stepPin0 2
#define motorInterfaceType0 1

#define dirPin1 5
#define stepPin1 4
#define motorInterfaceType1 1
//
//#define dirPin2 7
//#define stepPin2 6
//#define motorInterfaceType2 1

// Create new instances of AccelStepper class:
AccelStepper stepper0 = AccelStepper(motorInterfaceType0, stepPin0, dirPin0);
AccelStepper stepper1 = AccelStepper(motorInterfaceType1, stepPin1, dirPin1);
//AccelStepper stepper2 = AccelStepper(motorInterfaceType2, stepPin2, dirPin2);

// Copy translated coordinates here:
float coordinate_list[147][2] = 
  {
    {167.55,252.177},
    {167.478,252.365},
    {166.505,255.08},
    {165.968,257.154},
    {165.926,257.331},
    {165.462,259.627},
    {165.286,261.755},
    {165.278,261.917},
    {165.252,263.858},
    {165.528,265.943},
    {165.554,266.089},
    {165.883,267.656},
    {166.683,269.693},
    {166.74,269.824},
    {167.334,271.045},
    {168.721,272.977},
    {168.811,273.091},
    {169.568,274.005},
    {171.589,275.776},
    {171.704,275.874},
    {172.532,276.518},
    {175.208,278.071},
    {175.352,278.153},
    {176.159,278.573},
    {179.499,279.85},
    {179.53,279.863},
    {180.371,280.153},
    {184.361,281.102},
    {185.086,281.256},
    {189.703,281.816},
    {190.189,281.869},
    {195.42,281.991},
    {195.698,281.994},
    {201.337,281.63},
    {201.701,281.581},
    {207.223,280.772},
    {207.889,280.631},
    {213.208,279.431},
    {214.211,279.139},
    {219.22,277.613},
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
    {250,250}               //Can be convenient to add homing coordinate at end of program to return cables to original lengths (Don't forget to add 1 to the numcoords).
  };

//------------------------------------------------------------------------------------------------
void setup() {
  // Begin serial communication:
  Serial.begin(115200);
  
  // Set the maximum speed in steps per second:
  stepper0.setMaxSpeed(2000);
  stepper1.setMaxSpeed(2000);
//  stepper2.setMaxSpeed(2000);
  
  // Find initial encoder values for zeroing
  tcaselect(0);
  output[0] = encoder0.getPosition();
  initPosition[0] = output[0];
  lastOutput[0] = output[0];
  position[0] = output[0];

  tcaselect(1);
  output[1] = encoder1.getPosition();
  initPosition[1] = output[1];
  lastOutput[1] = output[1];
  position[1] = output[1];

//  tcaselect(2);
//  output[2] = encoder2.getPosition();
//  initPosition[2] = output[2];
//  lastOutput[2] = output[2];
//  position[2] = output[2];
}

//------------------------------------------------------------------------------------------------
void loop() {
  Serial.println("Requested Location");.
  for(int i=0; i<2; i++)  {
    requestedLocation[i] = coordinate_list[counter][i];
    Serial.println(requestedLocation[i]);  
  }
  if (counter == 0){
    delay(10000);
  }
  delay(5000);
  boolean flag0 = false;
  boolean flag1 = false;
//  flag2 = true;
  while (flag0 == false || flag1 == false){  
    // Monitor encoder position
    tcaselect(0);                             // get the raw values of the encoders
    output[0] = encoder0.getPosition();           
    tcaselect(1);
    output[1] = encoder1.getPosition();
//    tcaselect(2);
//    output[2] = encoder2.getPosition();

    if ((lastOutput[0] - output[0]) > 2047 )       // check if a full rotation has been made
      revolutions[0]++;
    if ((lastOutput[0] - output[0]) < -2047 )
      revolutions[0]--;
    if ((lastOutput[1] - output[1]) > 2047 )        
      revolutions[1]++;
    if ((lastOutput[1] - output[1]) < -2047 )
      revolutions[1]--;
//    if ((lastOutput[2] - output[2]) > 2047 )        
//      revolutions[2]++;
//    if ((lastOutput[2] - output[2]) < -2047 )
//      revolutions[2]--;
      
    currentPosition[0] = (-revolutions[0] * 4096 - output[0] + initPosition[0])* 0.087890625;   // calculate the position *IN DEGREES* the the encoder is at based off of the number of revolutions
    currentLocation[0] = startLength[0] + (currentPosition[0]/360)*2*M_PI*pulleyRadius;
    printLength[0] = currentLocation[0];
    currentPosition[1] = (-revolutions[1] * 4096 - output[1] + initPosition[1])* 0.087890625;   // calculate the position *IN DEGREES* the the encoder is at based off of the number of revolutions
    currentLocation[1] = startLength[1] + (currentPosition[1]/360)*2*M_PI*pulleyRadius;
    printLength[1] = currentLocation[1];
//    currentPosition[2] = (-revolutions[2] * 4096 - output[1] + initPosition[2])* 0.087890625;   // calculate the position *IN DEGREES* the the encoder is at based off of the number of revolutions
//    currentLocation[2] = startLength[2] + (currentPosition[2]/360)*2*M_PI*pulleyRadius;
//    printLength[2] = currentLocation[2];
        
    Serial.println("Location:");
    Serial.println(printLength[0]);
    Serial.println(printLength[1]);
//    Serial.println(printLength[2]);
    
    lastOutput[0] = output[0];                      // save the last raw value for the next loop 
    lastOutput[1] = output[1];
//    lastOutput[2] = output[2];
    
    // Set the speed in steps per second:
    speed0 = -100;
    speed1 = -100;
//    speed2 = -100;
    stepper0.setSpeed(speed0);
    stepper1.setSpeed(speed1);
//    stepper2.setSpeed(speed2);
    // Run steppers until position reached
    locationDiff[0] = currentLocation[0] - requestedLocation[0];      // check length
    if (locationDiff[0] < 0) {
      speed0 = -speed0;
      stepper0.setSpeed(speed0);
    }
    locationDiff[1] = currentLocation[1] - requestedLocation[1];      
    if (locationDiff[1] < 0) {
      speed1 = -speed1;
      stepper1.setSpeed(speed1);
    }
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

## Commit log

2023-07-28 Create arduino sketches folder
2023-07-28 Main sketch for G-Code coordinates on 3 pulleys
2023-07-28 Create STL files folder
